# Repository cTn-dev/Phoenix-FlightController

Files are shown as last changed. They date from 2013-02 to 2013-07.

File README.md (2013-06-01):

Flight Controller based on K20DX128 (Teensy 3.0)
------------------------------------------------

PIN setup (Teensy 3.0 pin numbering)
------------------------------------
  - I2C SCL 19
  - I2C SDA 18
  
  - PPM in (receiver) 3
  
  - Rotor 1 22
  - Rotor 2 23
  - Rotor 3 9
  - Rotor 4 10
  - Rotor 5 6
  - Rotor 6 20
  - Rotor 7 21
  - Rotor 8 5
  
  - Orientation lights / Armed-Disarmed indicator 14
  
  - Battery Monitor (current sensor) 17
  
Filters, kinematics, data handling
----------------------------------
  - Initial raw data from sensors (read every 1ms = 1000Hz) is being averaged by a simple averaging filter
  - Averaged data from sensors are being processed every 10ms (100Hz)
  - CMP kinematitcs (my own) selected by default
  - ARG kinematics (from aeroquad) is also supported (can be enabled by simple include change)
  - DCM kinematics (from FreeIMU)
  - Flight controller supports
    - Rate (ACRO) | gyro only
    - Attitude | gyro with accel corrections
    - Altitute hold | barometer or sonar
  - Pilot commands are being read by PPM sampling code via single PIN (with HW timer), both PPM and PWM in is supported
  - Stabilization and pilot commands are mixed together by 2 separate PID controllers
    - First (only used in attitude mode) mixes pilot commands with kinematics output
    - Second (used in both attitude and rate mode) mixes output from first PID or raw stick input with gyroRate output
  - For ESC signal output i am using an build in 8 channel FLEX timer (yes you can controll octocopter with this)
    - ESC PWM signal supports both 250Hz and 400Hz update rate (running at 400Hz by default)

Accelerometer offset trimming via TX
------------------------------------
  - While in dis-armed state
  - To enter the trimming mode = Throttle stick UP & Rudder LEFT
  - To adjust the values = PITCH UP & DOWN || ROLL LEFT & RIGHT
  - To save the values in EEPROM = Throttle UP & Rudder RIGHT 
    - (you dont have to save the values right away, you can test them, then return back to trimming mode and save them)
  - To leave trimming mode = Throttle stick DOWN

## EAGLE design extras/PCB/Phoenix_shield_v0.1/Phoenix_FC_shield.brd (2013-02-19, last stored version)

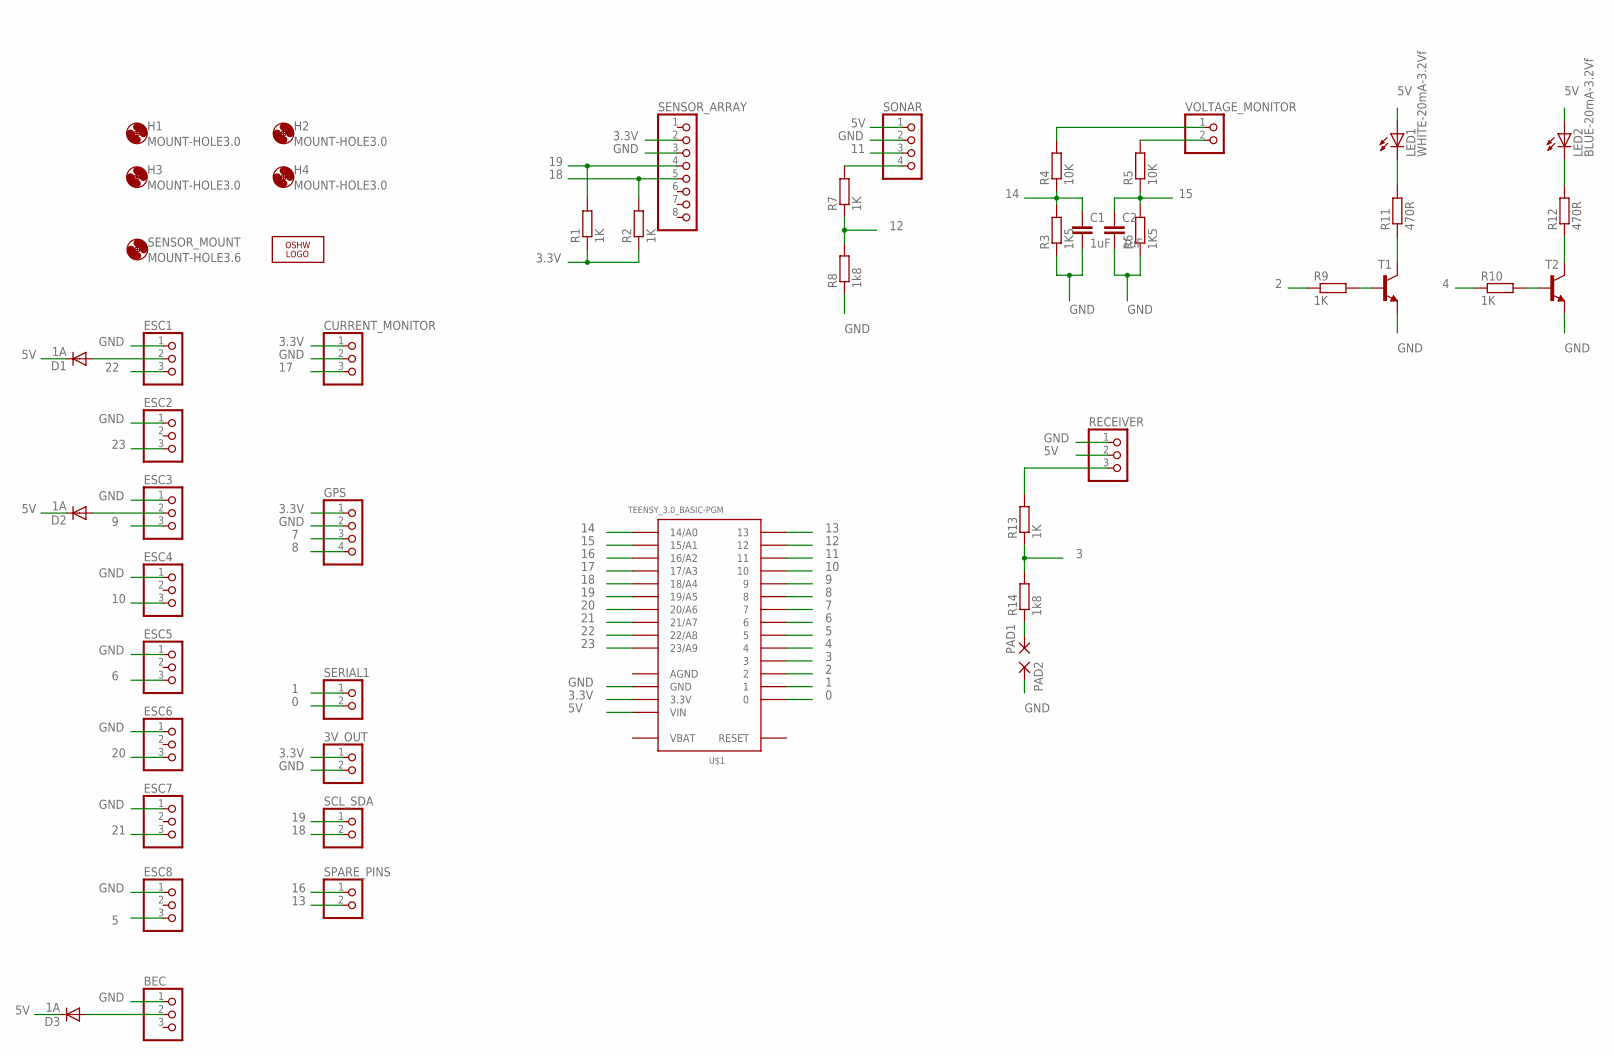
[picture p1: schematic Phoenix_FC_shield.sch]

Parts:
3V_OUT: PINHD-1X2; 1X02
BEC: PINHD-1X3; 1X03
C1, C2: 1uF; C0805
CURRENT_MONITOR: PINHD-1X3; 1X03
D1, D2, D3: 1A; DO-214AC
ESC1, ESC2, ESC3, ESC4, ESC5, ESC6, ESC7, ESC8: PINHD-1X3; 1X03
GPS: PINHD-1X4; 1X04
H1, H2, H3, H4: MOUNT-HOLE3.0; 3,0
LED1: WHITE-20mA-3.2Vf; CHIP-LED0805
LED2: BLUE-20mA-3.2Vf; CHIP-LED0805
LOGO1: OSHW_LOGO_8MILX0200-NT; OSHW_8X200_NOTEXT
PAD1, PAD2: WIREPADSMD1,27-254; SMD1,27-2,54
R1, R2, R7, R9, R10, R13: 1K; R0805
R3, R6: 1K5; R0805
R4, R5: 10K; R0805
R8, R14: 1k8; R0805
R11, R12: 470R; R0805
RECEIVER: PINHD-1X3; 1X03
SCL_SDA: PINHD-1X2; 1X02
SENSOR_ARRAY: PINHD-1X8; 1X08
SENSOR_MOUNT: MOUNT-HOLE3.6; 3,6
SERIAL1: PINHD-1X2; 1X02
SONAR: PINHD-1X4; 1X04
SPARE_PINS: PINHD-1X2; 1X02
T1, T2: BC817-40SMD; SOT23-BEC
U$1: TEENSY_3.0_BASIC-PGM
VOLTAGE_MONITOR: PINHD-1X2; 1X02

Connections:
0: SERIAL1.2, U$1.0
1: SERIAL1.1, U$1.1
2: R9.1, U$1.2
3: R13.1, R14.2, U$1.3
3.3V: 3V_OUT.1, CURRENT_MONITOR.1, GPS.1, R1.1, R2.1, SENSOR_ARRAY.2, U$1.3.3V, U$1.3.3V1 (3.3V)
4: R10.1, U$1.4
5: ESC8.3, U$1.5
5V: D1.C, D2.C, D3.C, LED1.A, LED2.A, RECEIVER.2, SONAR.1, U$1.VIN
6: ESC5.3, U$1.6
7: GPS.3, U$1.7
8: GPS.4, U$1.8
9: ESC3.3, U$1.9
10: ESC4.3, U$1.10
11: SONAR.3, U$1.11
12: R7.1, R8.2, U$1.12
13: SPARE_PINS.2, U$1.13
14: C1.1, R3.2, R4.1, U$1.14/A0
15: C2.1, R5.1, R6.2, U$1.15/A1
16: SPARE_PINS.1, U$1.16/A2
17: CURRENT_MONITOR.3, U$1.17/A3
18: R2.2, SCL_SDA.2, SENSOR_ARRAY.5, U$1.18/A4
19: R1.2, SCL_SDA.1, SENSOR_ARRAY.4, U$1.19/A5
20: ESC6.3, U$1.20/A6
21: ESC7.3, U$1.21/A7
22: ESC1.3, U$1.22/A8
23: ESC2.3, U$1.23/A9
AGND: U$1.AGND
GND: 3V_OUT.2, BEC.1, C1.2, C2.2, CURRENT_MONITOR.2, ESC1.1, ESC2.1, ESC3.1, ESC4.1, ESC5.1, ESC6.1, ESC7.1, ESC8.1, GPS.2, PAD2.1, R3.1, R6.1, R8.1, RECEIVER.1, SENSOR_ARRAY.3, SONAR.2, T1.E, T2.E, U$1.GND, U$1.GND1 (GND)
unnamed: R5.2, VOLTAGE_MONITOR.2
unnamed: R7.2, SONAR.4
unnamed: R11.1, T1.C
unnamed: R9.2, T1.B
unnamed: D2.A, ESC3.2
unnamed: PAD1.1, R14.1
unnamed: R4.2, VOLTAGE_MONITOR.1
unnamed: R10.2, T2.B
unnamed: R12.1, T2.C
unnamed: LED1.C, R11.2
unnamed: LED2.C, R12.2
unnamed: D1.A, ESC1.2
unnamed: R13.2, RECEIVER.3
unnamed: BEC.2, D3.A
VBAT: U$1.VBAT

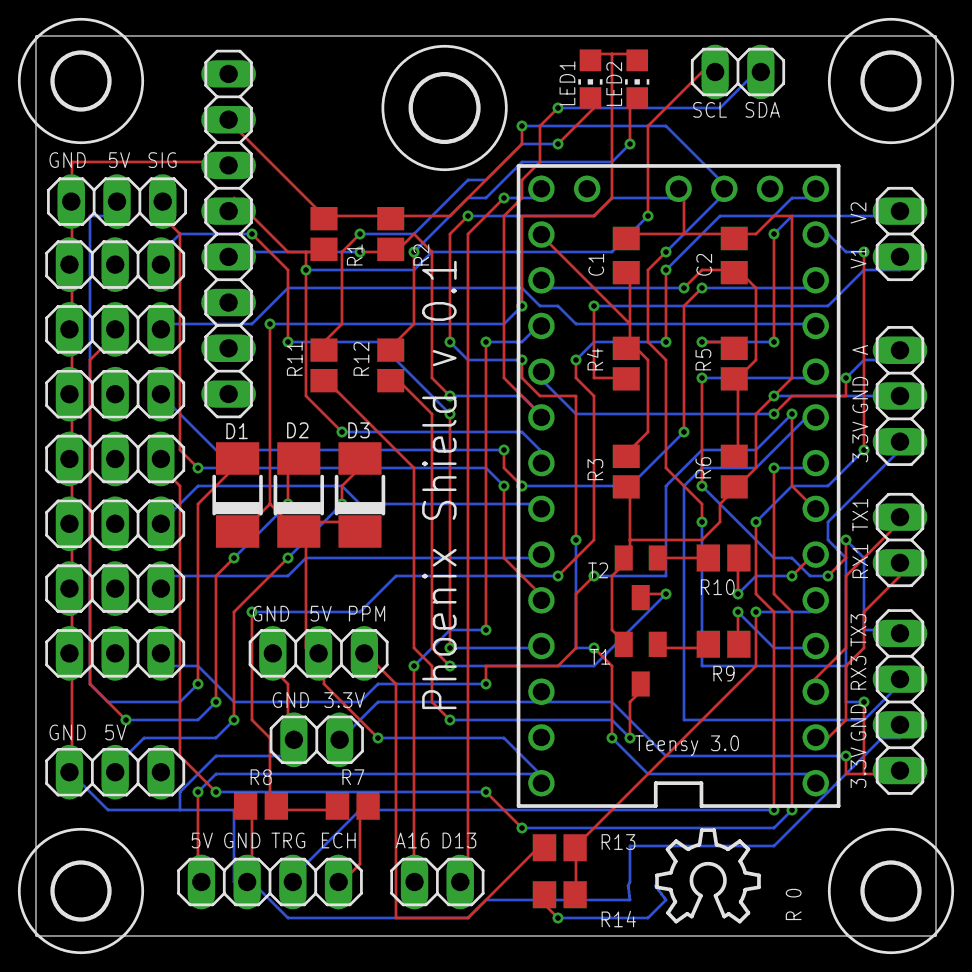
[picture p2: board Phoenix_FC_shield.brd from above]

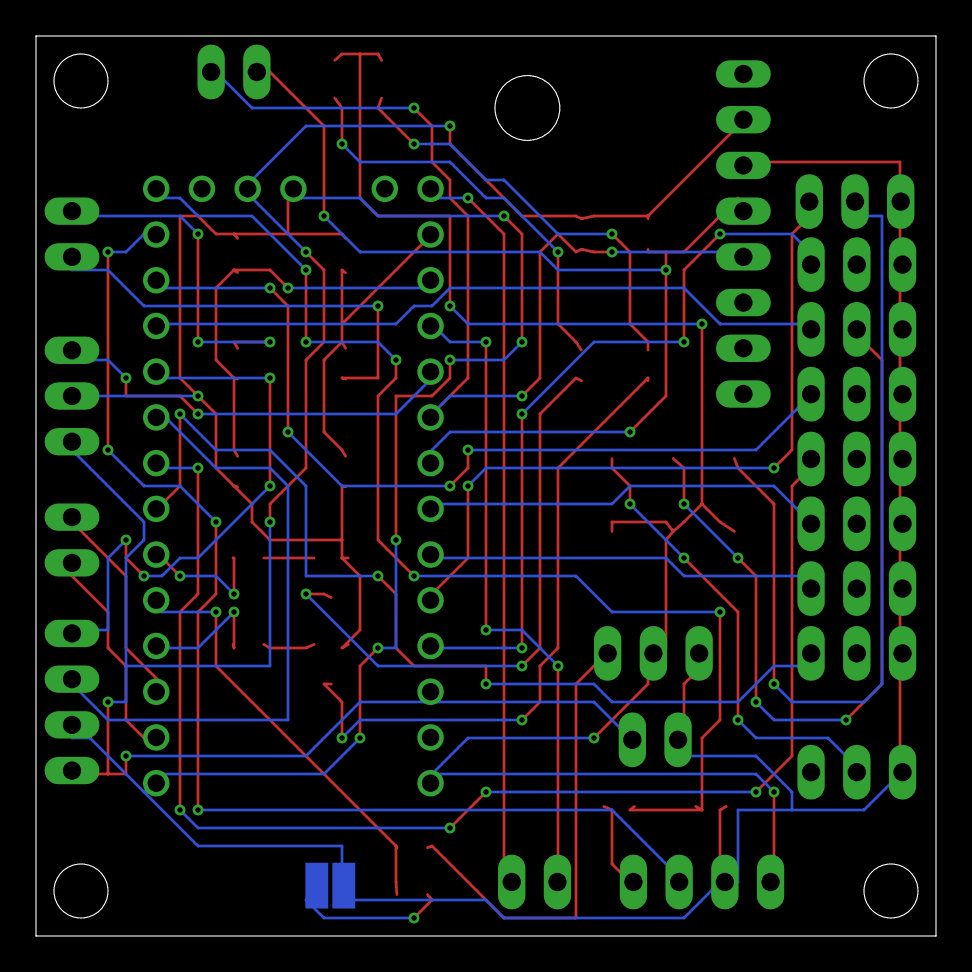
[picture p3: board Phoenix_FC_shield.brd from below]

Board: 2 copper layers, 50.0 x 50.0 mm, 51 parts (2 on the bottom side), 41 nets.

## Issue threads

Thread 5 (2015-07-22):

Run with overclocked compile?

enjoychang, 2015-07-22:
Looks like this firmware only works with maximum 72MHz Compilation.
Any progress on updated code for overclocked compilations, like 96 or 120 MHz?

Thanks.

CopterFail, 2015-07-23:
Ctn use i2c with too high speed - this may be a problem with higher clocks.

cTn-dev, 2015-07-23:
Unfortunately i don't work on this project for a very long time so i can't really answer this, however what @CopterFail seems reasonable, the prescalers will go a bit crazy with cpu overclock, so you will have to compensate for that.

enjoychang, 2015-07-23:
OK. Thanks, that make sense.
Also I found the pwm output for esc doesn’t work with overclock either.

Chang

Chang Liu
Aeronautics, Astronautics and Computational Engineering Group
Faculty of Engineering and the Environment
Engineering Centre of Excellence
Building 176, Room 5001, Table 103
Boldrewood Campus
University of Southampton
Southampton SO16 7QF
Mobile: +44(0)7859400775

Background:

https://sites.google.com/site/changliuuav/home
http://www.southampton.ac.uk/engineering/postgraduate/research_students/cl21g11.page?#background
http://blog.soton.ac.uk/robotics/
https://www.linkedin.com/profile/view?id=151520195&trk=nav_responsive_tab_profile

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

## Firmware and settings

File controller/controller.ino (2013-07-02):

/*
    Phoenix flight controller was initially build to support only one array of sensors but
    with minor sensor changes it seemed like a waste to just "drop" previous sensor support
    with this idea in mind i will try to make the flight controller feature set flexible as
    possible to accommodate as much hw as possible.

    Defines below only enable/disable "pre-defined" hw setups, you can always define your own
    setup in the == Hardware setup == section.
*/

// Arduino standard library imports
#include <Arduino.h>
#include <Wire.h>
#include <EEPROM.h>

// Custom imports
#include "controller.h"
#include "sensors.h"
#include "math.h"
#include "PID.h"
#include "dataStorage.h"

// == Hardware setup/s == 
#define PHOENIX_SHIELD_V_01
//#define AQ_SHIELD_V_20
//#define AQ_SHIELD_V_21

#ifdef PHOENIX_SHIELD_V_01
    // Led defines
    #define LED_WHITE 2
    #define LED_BLUE 4
    #define LED_ARDUINO 13
    
    // Features requested
    #define Magnetometer
    #define AltitudeHoldBaro
    #define BatteryMonitorCurrent
    #define GPS
    
    // Critical sensors on board (gyro/accel)
    #include <mpu6050_10DOF_stick_px01.h>
    
    // Magnetometer
    #include <Magnetometer_HMC5883L.h>
    
    // Barometer
    #include <Barometer_ms5611.h>
    
    // GPS (ublox neo 6m)
    #include <GPS_ublox.h>
    
    // Current sensor
    #include <BatteryMonitor_current.h>
    
    // Kinematics used
    #include <kinematics_CMP.h>
    
    // Receiver
    #include <Receiver_teensy3_HW_PPM.h>
    
    // Frame type definition
    #include <FrameType_QuadX.h> 

    // Motor / ESC setup
    #define ESC_400HZ
    #include <ESC_teensy3_HW.h>     
#endif

#ifdef AQ_SHIELD_V_20
    // Led defines
    #define LED_ARDUINO 13
    
    // Features requested
    #define Magnetometer
    
    // Critical sensors on board (gyro/accel)
    #include <ITG3200_AQ_v20.h>
    #include <BMA180_AQ_v20.h>
    
    // Magnetometer
    #include <Magnetometer_HMC5883L.h>
    
    // Kinematics used
    #include <kinematics_CMP.h>
    
    // Receiver
    #include <Receiver_328p_HW_PPM.h> // this is just temporary, this shield requires proper mega 1280 2560 support
    
    // Frame type definition
    #include <FrameType_QuadX.h> 

    // Motor / ESC setup
    #include <ESC_328p_HW.h> // this is just temporary, this shield requires proper mega 1280 2560 support      
#endif

#ifdef AQ_SHIELD_V_21
    // Led defines
    #define LED_ARDUINO 13
    
    // Features requested
    #define Magnetometer
    
    // Critical sensors on board (gyro/accel)
    #include <ITG3200_AQ_v21.h>
    #include <ADXL345_AQ_v21.h>
    
    // Magnetometer
    #include <Magnetometer_HMC5883L.h>
    
    // Kinematics used
    #include <kinematics_CMP.h>
    
    // Receiver
    #include <Receiver_328p_HW_PPM.h> // this is just temporary, this shield requires proper mega 1280 2560 support
    
    // Frame type definition
    #include <FrameType_QuadX.h> 

    // Motor / ESC setup
    #include <ESC_328p_HW.h> // this is just temporary, this shield requires proper mega 1280 2560 support     
#endif
// == END of Hardware setup ==

// Global PID object definitions
PID yaw_command_pid;
PID pitch_command_pid;
PID roll_command_pid;

PID yaw_motor_pid;
PID pitch_motor_pid;
PID roll_motor_pid;

#ifdef AltitudeHoldBaro
PID altitude_hold_baro_pid;
#endif

#ifdef AltitudeHoldSonar    
PID altitude_hold_sonar_pid;
#endif

#ifdef GPS
PID yaw_position_hold_pid;
PID pitch_position_hold_pid;
PID roll_position_hold_pid;
#endif  

// Function to reset I terms inside PID objects
void reset_PID_integrals() {
    yaw_command_pid.IntegralReset();
    pitch_command_pid.IntegralReset();
    roll_command_pid.IntegralReset();
    
    yaw_motor_pid.IntegralReset();
    pitch_motor_pid.IntegralReset();
    roll_motor_pid.IntegralReset();
    
    #ifdef AltitudeHoldBaro
    altitude_hold_baro_pid.IntegralReset();
    #endif
    
    #ifdef AltitudeHoldSonar
    altitude_hold_sonar_pid.IntegralReset();
    #endif      
}
  
// Include this last as it contains objects from previous declarations
#include "GPS.h"
#include "PilotCommandProcessor.h"
#include "SerialCommunication.h"  
  
void setup() {
    // PIN settings
    pinMode(LED_ARDUINO, OUTPUT);
    
#ifdef LED_WHITE
    pinMode(LED_WHITE, OUTPUT);
#endif

#ifdef LED_BLUE
    pinMode(LED_BLUE, OUTPUT);
#endif

    // Initialize serial communication
    Serial.begin(38400); // Virtual USB Serial on teensy 3.0 is always 12 Mbit/sec (can be initialized with baud rate 0)

#ifdef GPS
    Serial3.begin(38400);
#endif
 
    // Join I2C bus as master
    Wire.begin();

    // I2C bus hardware specific settings
#if defined(__MK20DX128__)
    I2C0_F = 0x00; // 2.4 MHz (prescaler 20)
    I2C0_FLT = 4;
#endif
    
#if defined(__AVR__)
    TWBR = 12; // 400 KHz (maximum supported frequency)
#endif
    
    // Read data from EEPROM to CONFIG union
    readEEPROM();
    
    // Initialize PID objects with data from EEPROM
    yaw_command_pid = PID(&headingError, &YawCommandPIDSpeed, &headingSetpoint, (float*) &CONFIG.data.PID_YAW_c);
    pitch_command_pid = PID(&kinematicsAngle[YAXIS], &PitchCommandPIDSpeed, &commandPitch, (float*) &CONFIG.data.PID_PITCH_c);
    roll_command_pid = PID(&kinematicsAngle[XAXIS], &RollCommandPIDSpeed, &commandRoll, (float*) &CONFIG.data.PID_ROLL_c);
    
    yaw_motor_pid = PID(&gyro[ZAXIS], &YawMotorSpeed, &YawCommandPIDSpeed, (float*) &CONFIG.data.PID_YAW_m);
    pitch_motor_pid = PID(&gyro[YAXIS], &PitchMotorSpeed, &PitchCommandPIDSpeed, (float*) &CONFIG.data.PID_PITCH_m);
    roll_motor_pid = PID(&gyro[XAXIS], &RollMotorSpeed, &RollCommandPIDSpeed, (float*) &CONFIG.data.PID_ROLL_m);  
    
#ifdef AltitudeHoldBaro
    altitude_hold_baro_pid = PID(&baroAltitudeToHoldTarget, &AltitudeHoldMotorSpeed, &baroAltitudeRunning, (float*) &CONFIG.data.PID_BARO);
#endif
    
#ifdef AltitudeHoldSonar
    altitude_hold_sonar_pid = PID(&sonarAltitudeToHoldTarget, &AltitudeHoldMotorSpeed, &sonarAltitude, (float*) &CONFIG.data.PID_SONAR);
#endif    
    
#ifdef GPS
    // yaw_position_hold_pid = PID();
    // pitch_position_hold = PID();
    // roll_position_hold = PID();
#endif
    
    // Initialize motors/receivers/sensors
    initializeESC();    
    initializeReceiver();
    
    sensors.initializeGyro();
    sensors.initializeAccel();
    
#ifdef Magnetometer
    sensors.initializeMag();
#endif
    
#ifdef AltitudeHoldBaro
    sensors.initializeBaro();    
#endif
    
#ifdef AltitudeHoldSonar
    initializeSonar();
#endif    
    
#ifdef GPS
    gps.initializeBaseStation();
#endif
    
    // All is ready, start the loop
    all_ready = true;
}

void loop() {   
    // Dont start the loop until everything is ready
    if (!all_ready) return; 
 
    // Used to measure loop performance
    itterations++;
    
    // Timer
    currentTime = micros();
    
    // Read data (not faster then every 1 ms)
    if (currentTime - sensorPreviousTime >= 1000) {
        sensors.readGyroSum();
        sensors.readAccelSum();        
        
#ifdef AltitudeHoldSonar
        // Bring sonar pin down (complete TLL trigger pulse)
        readSonarFinish();
#endif    
        
        sensorPreviousTime = currentTime;
    }    
    
    // 100 Hz task loop (10 ms)
    if (currentTime - previousTime > 10000) {
        frameCounter++;
        
        process100HzTask();
        
        // 50 Hz tak (20 ms)
        if (frameCounter % TASK_50HZ == 0) {
            process50HzTask();
        }
        
        // 10 Hz task (100 ms)
        if (frameCounter % TASK_10HZ == 0) {
            process10HzTask();
        }  
        
        // 1 Hz task (1000 ms)
        if (frameCounter % TASK_1HZ == 0) {
            process1HzTask();
        }
        
        // Reset frameCounter back to 0 after reaching 100 (1s)
        if (frameCounter >= 100) {
            frameCounter = 0;
        }
        
        previousTime = currentTime;
    }
}

void process100HzTask() {    
    sensors.evaluateGyro();
    sensors.evaluateAccel();
    
#ifdef AltitudeHoldBaro
    // Baro is being sampled every 10ms (because measuring pressure is slow) 
    sensors.readBaroSum();
#endif    
    
#ifdef GPS
    sensors.readGPS();
#endif

    // Listens/read Serial commands on Serial1 interface (used to pass data from configurator)
    readSerial();
    
    // Update kinematics with latest data
    kinematics_update(gyro[XAXIS], gyro[YAXIS], gyro[ZAXIS], accel[XAXIS], accel[YAXIS], accel[ZAXIS]);
    
    // Update heading
    headingError = kinematicsAngle[ZAXIS] - commandYawAttitude;
    NORMALIZE(headingError); // +- PI
    
    // Update PIDs according the selected mode
    if (flightMode == ATTITUDE_MODE) {
        // Compute command PIDs (with kinematics correction)
        yaw_command_pid.Compute();
        pitch_command_pid.Compute();
        roll_command_pid.Compute();
    } else if (flightMode == RATE_MODE) {
        // Stick input, * 4.0 is the rotation speed factor
        YawCommandPIDSpeed = commandYaw * 4.0;
        PitchCommandPIDSpeed = commandPitch * 4.0;
        RollCommandPIDSpeed = commandRoll * 4.0;        
    }   
    
    // Compute motor PIDs (rate-based)    
    yaw_motor_pid.Compute();
    pitch_motor_pid.Compute();
    roll_motor_pid.Compute();     
    
    // This is the place where the actual "force" gets applied
    if (armed) {
        if (TX_throttle >= CONFIG.data.minimumArmedThrottle) { // disable stabilization if throttle is very low
            updateMotorsMix(); // Frame specific motor mix
        } else {
            // Set all motors to minimum armed throttle
            for (uint8_t i = 0; i < MOTORS; i++) {
                MotorOut[i] = CONFIG.data.minimumArmedThrottle;
            }
        }
        updateMotors(); // Update ESCs
    } 
}

void process50HzTask() {
    processPilotCommands();
    
#ifdef AltitudeHoldBaro
    sensors.evaluateBaroAltitude();
#endif   

#ifdef LED_WHITE
    // Blink "aircraft beacon" LED
    if ((Beacon_LED_state == 51) || (Beacon_LED_state == 59) || (Beacon_LED_state == 67)) {
        digitalWrite(LED_WHITE, HIGH);
    } else {
        digitalWrite(LED_WHITE, LOW);
    }

    Beacon_LED_state++;
    
    if (Beacon_LED_state >= 100) {
        Beacon_LED_state = 0;
    }
#endif
}

void process10HzTask() {
    // Trigger RX failsafe function every 100ms
    RX_failSafe();
    
#ifdef AltitudeHoldSonar
    // Request sonar reading
    readSonar();
#endif    
    
#ifdef Magnetometer
    sensors.readMag();
    sensors.evaluateMag();
#endif
    
#ifdef BatteryMonitorCurrent
    readBatteryMonitorCurrent();
#endif   
    
    // Print itterations per 100ms
#ifdef DISPLAY_ITTERATIONS
    Serial.println(itterations);
#endif
    
    // Blink integrated arduino LED
    Arduino_LED_state = !Arduino_LED_state;
    digitalWrite(LED_ARDUINO, Arduino_LED_state);   
    
    // Reset Itterations
    itterations = 0;    
}

void process1HzTask() {   
#ifdef LED_BLUE
    // Armed/ Dis-armed indicator
    if (armed) {
        digitalWrite(LED_BLUE, HIGH);
    } else {
        digitalWrite(LED_BLUE, LOW);
    }
#endif
}

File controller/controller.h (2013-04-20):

// Main loop variables
unsigned long currentTime = 0;
unsigned long previousTime = 0;
unsigned long sensorPreviousTime = 0;
uint8_t frameCounter = 0;
uint32_t itterations = 0;

bool all_ready = false;
bool armed = false;
bool flightMode = false;
bool altitudeHoldBaro = false;
bool altitudeHoldSonar = false;
bool positionHoldGPS = false;

// Flight modes
#define RATE_MODE 0
#define ATTITUDE_MODE 1

// Primary channel definitions
#define ROLL        0
#define PITCH       1
#define THROTTLE    2
#define YAW         3

// PID pseudo definitions
#define P  0 // Proportional
#define I  1 // Integral
#define D  2 // Derivative
#define WG 3 // WindupGuard

// Axis definitions
#define XAXIS 0
#define YAXIS 1
#define ZAXIS 2

// Arbitrary ON/OFF definitions
#define OFF 0
#define ON 1

// Blinking LED to indicate activity
bool Arduino_LED_state = 0;
uint8_t Beacon_LED_state = 0;

// Modulo definitions (integer remainder)
#define TASK_50HZ 2
#define TASK_10HZ 10
#define TASK_1HZ 100

// Kinematics variable defnitions
float kinematicsAngle[3];

// FlightController commands definitions
float commandYaw, commandYawAttitude, commandPitch, commandRoll, commandThrottle;

// Heading related variables
float headingError = 0.0;
float headingSetpoint = 0.0;

// PID variables
float YawCommandPIDSpeed, PitchCommandPIDSpeed, RollCommandPIDSpeed;
float YawMotorSpeed, PitchMotorSpeed, RollMotorSpeed, AltitudeHoldMotorSpeed;
int16_t throttle = 1000;

// +- PI normalization macro
#define NORMALIZE(x) do { if ((x) < -PI) (x) += 2 * PI; else if ((x) > PI) (x) -= 2 * PI; } while (0);

// Custom definitions
//#define DISPLAY_ITTERATIONS

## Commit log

2012-12-11 initial commit
    RX HW sampling and PWM servo generation is currently broken
    [controller.ino]
2012-12-14 Working PPM sampling
    ESC servo PWM signal generation still in beta stage
2012-12-14 PWM fixes
2012-12-14 PPM sampling buffering and sanity checks
    thist step might not be necessary, but its great that we have the
    ability to discard corrupted frame (which could cause some really things
    later on)
2012-12-15 Better kinematics documentation
    + some simple variables rename (for clarity)
2012-12-15 PPM doc, RX failsafe + auto descend
    [controller.ino]
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2012-12-16 auto disarm after throttle reaches 1000us (0)
2012-12-16 Manual accel offset calibration
2012-12-16 force attitude mode on failsafe
    i am also considering setting yaw/pitch/roll to 0/middle, but will see
    how this goes
2012-12-17 BIG changes to the sensor data handling
    did a rather long flight test, everything seems to be running smooth
2012-12-19 Slowing down status/orientation LEDs
    Just moving the LED code from 10hz to 1hz loop (orientation LEDs
    blinking 5x/s in dis-armed mode was really painful to watch)
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2012-12-21 Battery monitor implementation
    + orientation lights are used to signal battery warning and battery
    state
    This needs serious polishing
2012-12-21 YAW angle build up "speed up"
2012-12-22 Battery monitor code cleanup + documentation
2012-12-22 more changes to the battery monitor
    (still some problems that need fixing)
2012-12-22 temporary disabling battery monitor
    (till the new current sensor arrives)
2012-12-23 cleanup & YAW stick angle speed up
2012-12-27 added teensy wire library to repo
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2012-12-28 visualization polish
    According to data visualization it seems there is still some improvement
    regarding accel fusion in kinematics
2012-12-29 Lowered accelerometer weight in CMP
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2013-01-02 cleanup, smoother (slower) gyro calibration
2013-01-03 accelerometer angle flip corrections
2013-01-04 kinematicsZ PI normalization and YAW corrections
    [PilotCommandProcessor.h, controller.h]
2013-01-05 differen't approach to improve sensor fusion
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2013-01-06 YAW fixes
2013-01-06 ability to reset Z axis in visualization
    [controller.ino]
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2013-01-08 some initial sonar fixes
    we might need a different throttle PID for sonar hold altitude, because
    the "standard" PID values that are used for baro doesn't apply in this
    case
    [PilotCommandProcessor.h, controller.h, controller.ino]
2013-01-08 IMPORTANT baro and sonar fixes
    [PilotCommandProcessor.h]
2013-01-09 partial commit introducing configuration file
    [configuration.h]
2013-01-09 finally dividing sensors into separate libraries
    [configuration.h]
2013-01-09 motor pin setup order change (for clarity)
2013-01-09 328p servo/ppm in HW support
    [configuration.h]
2013-01-10 moving rx failsafe to the main contoller file
    [controller.ino]
2013-01-10 initial register support for older sensors
2013-01-10 baro/sonar PID changes
    Baro and sonar now uses different PIDs, also by disabling baro/sonar the
    PID objects are removed which helps reduce sketch size on older
    platforms
2013-01-10 cleanup & needs a better folder structure
    [configuration.h]
2013-01-11 object oriented i2c sensor base
    srf04 isn't part of this sensor array
2013-01-11 YAW angle flip bugfix
    [PilotCommandProcessor.h]
2013-01-11 made the PID throttle correction range bigger
    still requires PID tuning, but its getting there
    [PilotCommandProcessor.h, controller.h, controller.ino]
2013-01-13 PID changes @ I2C timeout testing
2013-01-13 I2C timeout disabled (for now)
2013-01-15 initial Ublox commit & mpu6050 i2c bypass
2013-01-16 initial magnetometer integration & wire lib fixes
    [controller.ino]
2013-01-16 i2c scanner in extras folder
2013-01-16 initial MS5611 sensor support (not working yet)
    [controller.ino]
2013-01-18 initial current monitor code
2013-01-19 full battery monitor current support
2013-01-19 HW specific I2C settings and some documentation
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2013-01-21 battery monitor current - improvements
2013-01-21 new sensor data storage structure (array based)
    also all kinematics now take sensor data via priority
    gyro => accel => mag => gps = > magic genie
2013-01-26 gyro calibration sanity checks
2013-01-26 multiple frames related changes
2013-01-26 current monitor bugfix
2013-01-27 arduino related name changes
2013-01-30 PID integral reset support
    [PilotCommandProcessor.h, controller.ino]
2013-01-30 typo fix and support for some basic OFF ON defines
    [controller.h]
2013-02-01 Adding support to ACCEL on dataStorage, fixing some indentation problems on ACCEL as well. Changed dataStorage include position so it can be accessed on other included files.
    [controller.ino, dataStorage.h]
2013-02-01 3,4,6,8 motor setup for teensy hw
2013-02-01 HW part of ESC calibration
2013-02-01 some alpha stage configurator communication code
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2013-02-06 initial switch to "ublox" style protocol
2013-02-08 some minor PID value changes
2013-02-08 back end changes related to accel calibration
2013-02-09 accel calibration handler
    both front end and back end are ready, however there is an Z axis
    calibration fix required (thats yet to be implemented)
    [SerialCommunication.h]
2013-02-09 announced Z axis calibration fix
2013-02-09 accelerometer calibration fixes
    seems to be perfect =)
2013-02-09 moved kinematics angles to array
2013-02-10 configurator motor output implemented
2013-02-10 more AVR related fixes
    [SerialCommunication.h]
2013-02-11 more AVR bugfixes.. oh
    [SerialCommunication.h, controller.ino]
2013-02-11 polishing PID tuning init in configurator
2013-02-11 avr related ublox fixes
    [controller.ino]
2013-02-11 esc calibration request bugfix
2013-02-12 switching from doubles to floats
    (significant performance boost), invsqrt disabled (untill all of the
    output issues gets resolved)
    [SerialCommunication.h, controller.h]
2013-02-12 cleanup and sqrt bugfixes
    [SerialCommunication.h]
2013-02-12 GPS PID fields in EEPROM
2013-02-13 400 and 250Hz PWM definitions
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2013-02-15 some different motor setup dis-armed fixes
    [controller.ino]
2013-02-15 ADXL AQ 2.1 bugfixes
    [controller.ino]
2013-02-15 yaw support in vehicle view
2013-02-15 lots of bugfixes in the sensor area
    [controller.ino]
2013-02-16 optimizing gyro calibration
    calibration works correctly for mpu6050, ITG3200 might need some testing
    [controller.ino]
2013-02-17 time bugfixes and cleanup
    [SerialCommunication.h, controller.ino]
2013-02-18 getting ESC 328p code more up to date
2013-02-19 PCB up
    [Phoenix_FC_shield.brd, Phoenix_FC_shield.sch]
2013-02-19 PCB - tiny resistor value changes
    [Phoenix_FC_shield.brd, Phoenix_FC_shield.sch]
2013-02-20 no more jDataView stuff in configurator
    [Phoenix_FC_shield.brd, Phoenix_FC_shield.sch]
2013-02-24 different alive led state handling
2013-02-24 speeding up the alive led blink rate
2013-02-28 stronger weight for accelerometer fusion
2013-03-01 configurator motor tab bugfixes
    [controller.ino, motor_output.js]
2013-03-02 the long awaited YAW fix for CMP kinematics
    [PilotCommandProcessor.h, controller.h, controller.ino]
2013-03-02 cleaning up CMP kinematics a little
2013-03-03 adding MAF filter to the extras folder
2013-03-03 optimizing motor output in serial com
2013-03-03 initial configurator code for motor commands
    inspired by Shadow6363
2013-03-04 configurator/fc motor command processing
2013-03-04 finishing touches to motor command handling
2013-03-04 optimizing hardcoded stuff in ESC calibration
2013-03-05 improving LED status support
2013-03-06 PWM Receiver support with HW timer for teensy 3.0
2013-03-07 documentation for PWM receiver
2013-03-12 polishing teensy 3.0 receiver code
2013-03-15 manual accelerometer offset tuning support
    feature proposed by ReadError
2013-03-16 fixing some precompiler indentation
    [PilotCommandProcessor.h, controller.h, controller.ino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]
2013-03-16 fixing some hidden bugs in serialcom
    [SerialCommunication.h]
2013-03-17 failsafe bugfix related to dynamic channel assig
    [controller.h]
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2013-03-19 YAW correction limited to max +-20%
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2013-03-25 Revert "experimental gyroscope overtime bias calibration"
    This reverts commit 199bb3f501250914fb9043802a42de9171bc3439.
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2013-04-04 configurator UI polish + some sensor bugfixes
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2013-04-10 one way protocol CRC check (union sending broken)
    [SerialCommunication.h, motor_output.js]
2013-04-10 crc failed response and send union working
    [SerialCommunication.h]
2013-04-14 motor output moved to the new data structure
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2013-04-20 getting failsafe code up to speed with dynam. AUX
    [PilotCommandProcessor.h, controller.h]
2013-04-20 correcting failsafe functionality with new AUX
    [PilotCommandProcessor.h]
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2013-04-21 fixing reverted pitch
    TX settings needs to be adjusted for this
    [PilotCommandProcessor.h]
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2013-04-23 Revert "optimized handling of "FAST" YAW commands"
    This reverts commit 3bb78803d9d9dd8c8448c6224ebc9d1b4e5daeb1.
    [PilotCommandProcessor.h]
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2013-05-11 Fully dynamic 16 channel receiver support 1/?
    With this commit, we might be officially forced to drop atmega168/328
    support because of the lack of resources required for the software to
    operate properly (current setup of fully scalable functions for 16
    channel receiver requires usage of 64bit variable for aux mask and
    function masks.
    This will most likely be "too much" for the 2KB of ram available on the
    mainstream atmega chips.
    [PilotCommandProcessor.h, SerialCommunication.h, dataStorage.h]
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2013-06-20 initial work on dynamic axis mapping
    dynamic axis mapping is added to the primary CONFIG_struct and data is
    being initialized/utilized only in mpu6050_10DOF_stick for now, when the
    configurator side of this functionality is implemented, i will
    redistribute this new code to all accel/gyro/mag libraries (lots of
    copying to be done)
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2013-07-02 workaround for "bouncy" landing
    [controller.ino]
